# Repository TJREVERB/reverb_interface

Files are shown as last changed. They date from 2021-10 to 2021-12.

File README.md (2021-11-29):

# TJREVERB Interface Boards
Interface board rework, moved from Eagle to Kicad

The board provides power connections from the EPS and data connections from the flight computer to various components.

APRS and Iridium (through a MAX3232) are connected to UART, and can be selected between hardware UART and software/converter UART using jumpers. software/converter UART uses a converter as the primary UART device, with an option for software bit banging using RPi GPIO as a backup.

There are three branches: USB to UART, SPI to UART (DEPRECATED IN v1.4), and Multicore

The first is similar to the original design, and uses a USB to UART converter. 

The second uses an SPI to UART converter so that we can send data through the main Pi header instead of pogo pins or USB pads. DEPRECATED DUE TO DIFFICULTY IN SOFTWARE IMPLEMENTATION

The third uses an external AVR microcontroller as a secondary core, to be used for IO operations, specifically as an SPI/I2C to UART converter and an I2C buffer for sending delayed commands to the EPS (e.g. sending bus reset after a delay to give the pi enough time to exit script)

All branches include connections to bitbang uart instead of using the converter.

## Versions
v1.0 initial

v1.1 routing improvements

v1.2 fabricated first, received 10/24/21

v1.3 adds major corrections for circuitry

v1.4 introduces the new multicore branch

v1.5 replaces LSM9DS1 IMU with BNO055

v1.6 adds RTC and battery

v2.0 CAD compatibility check, fabbed as v2 on 11/28/21

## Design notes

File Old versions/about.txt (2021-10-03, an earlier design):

These were designed in eagle. Rev5 was fabricated and is currently in use in the flatsat.

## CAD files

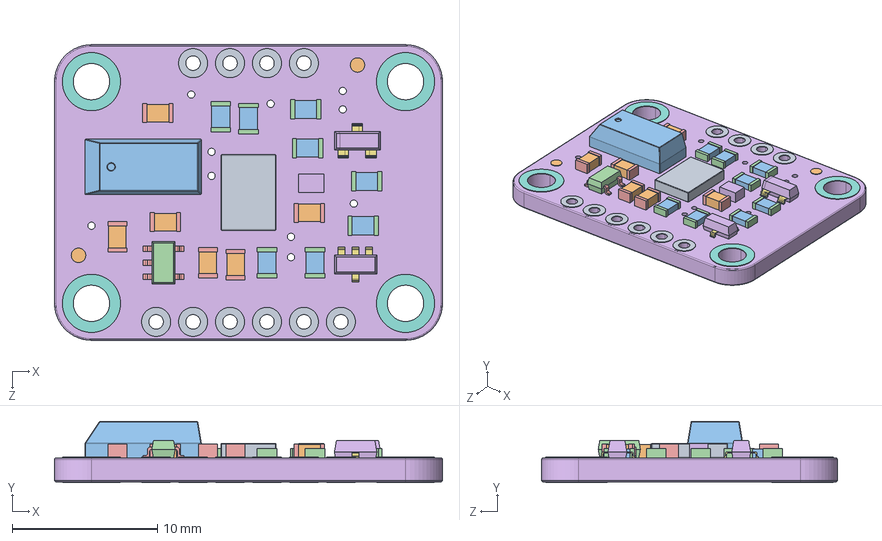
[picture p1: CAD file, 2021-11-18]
REVERB Interface Multicore/3D/Adafruit_BNO055_AP203.STEP
26.7 x 4.20 x 20.3 mm

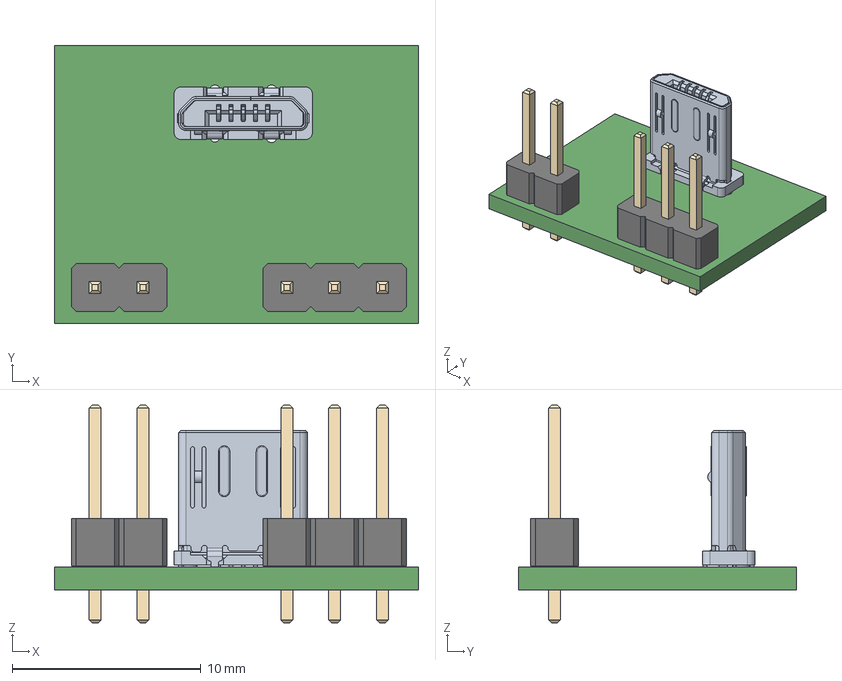
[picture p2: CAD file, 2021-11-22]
uUSB male BOB/uUSB male BOB.step
19.3 x 14.7 x 11.5 mm

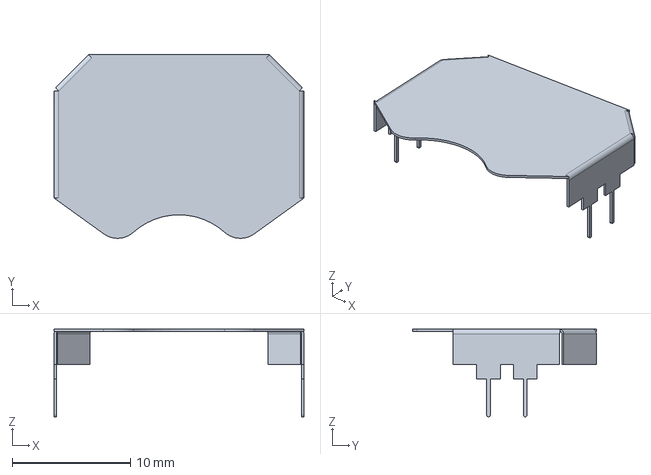
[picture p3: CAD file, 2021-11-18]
REVERB Interface Multicore/3D/Linx_-_BAT-HLD-001-THM.step
21.1 x 15.5 x 7.40 mm

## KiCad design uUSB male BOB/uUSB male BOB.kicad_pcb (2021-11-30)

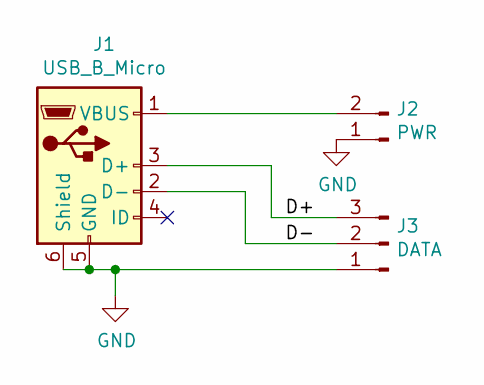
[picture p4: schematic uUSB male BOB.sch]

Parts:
J1: USB_B_Micro; USB3150-30-130-A
J2: PWR; PinHeader_1x02_P2.54mm_Vertical
J3: DATA; PinHeader_1x03_P2.54mm_Vertical

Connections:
/D+: J1.3 (D+), J3.3
/D-: J1.2 (D-), J3.2
GND: J1.5 (GND), J1.6 (Shield), J2.1, J3.1
unnamed: J1.1 (VBUS), J2.2

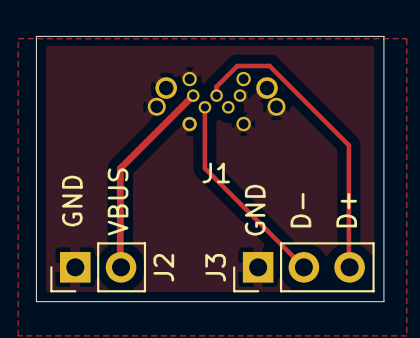
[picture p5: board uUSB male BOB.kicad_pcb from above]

Board: 2 copper layers, 19.3 x 14.7 mm, 3 parts (0 on the bottom side), 4 nets.

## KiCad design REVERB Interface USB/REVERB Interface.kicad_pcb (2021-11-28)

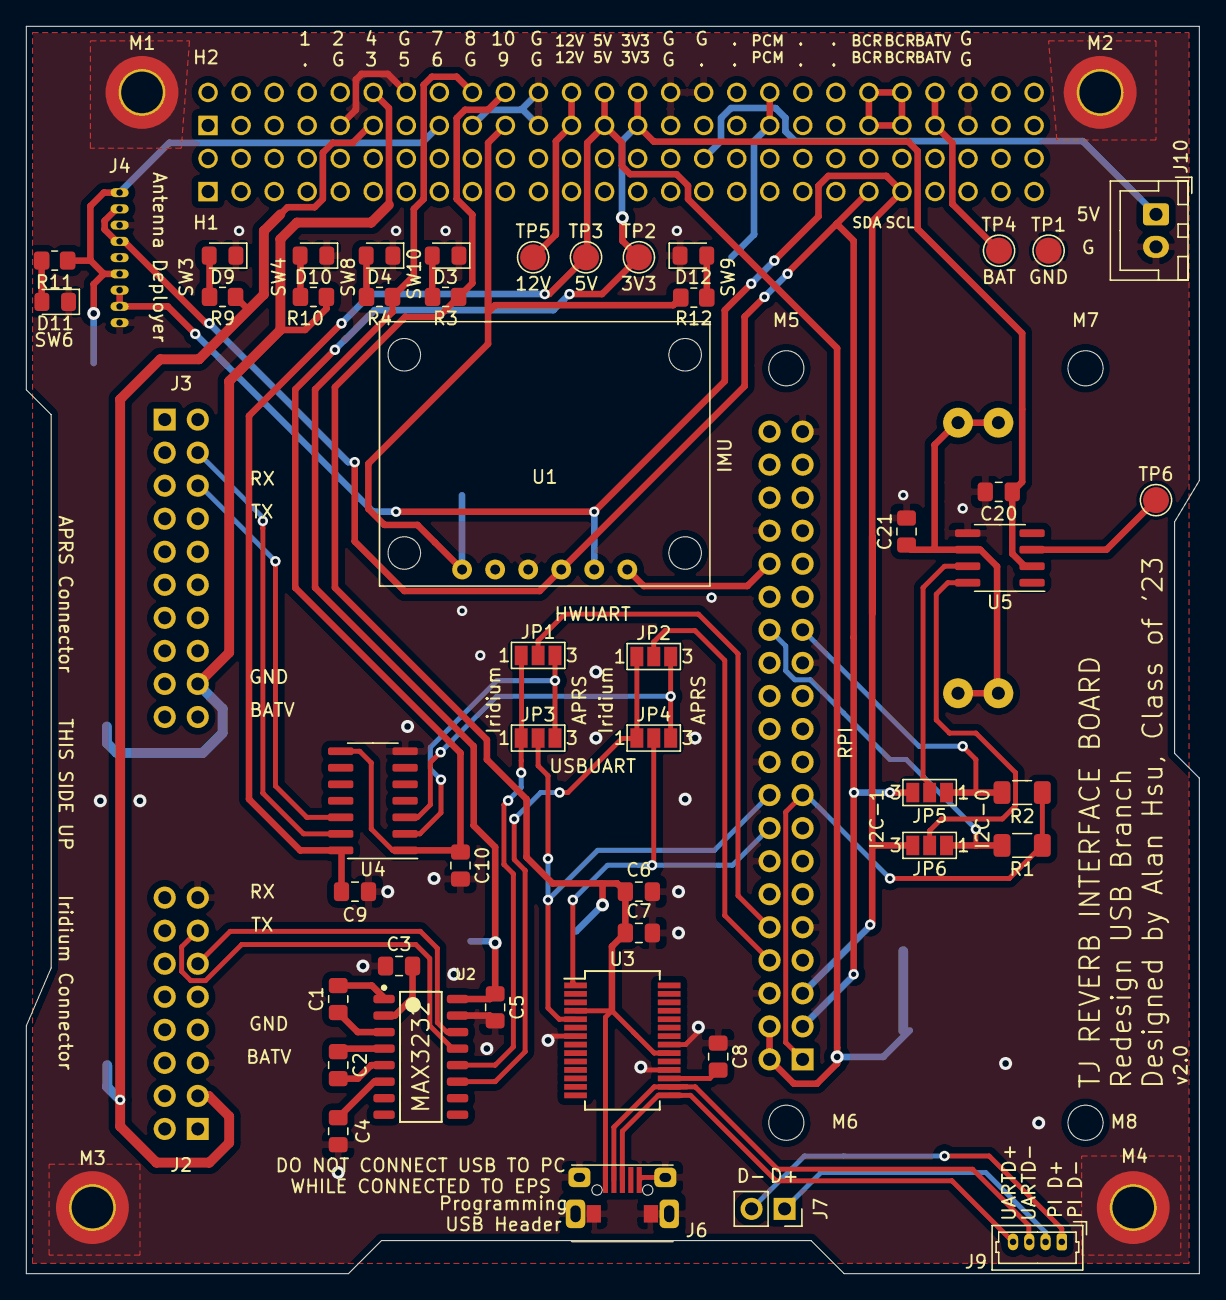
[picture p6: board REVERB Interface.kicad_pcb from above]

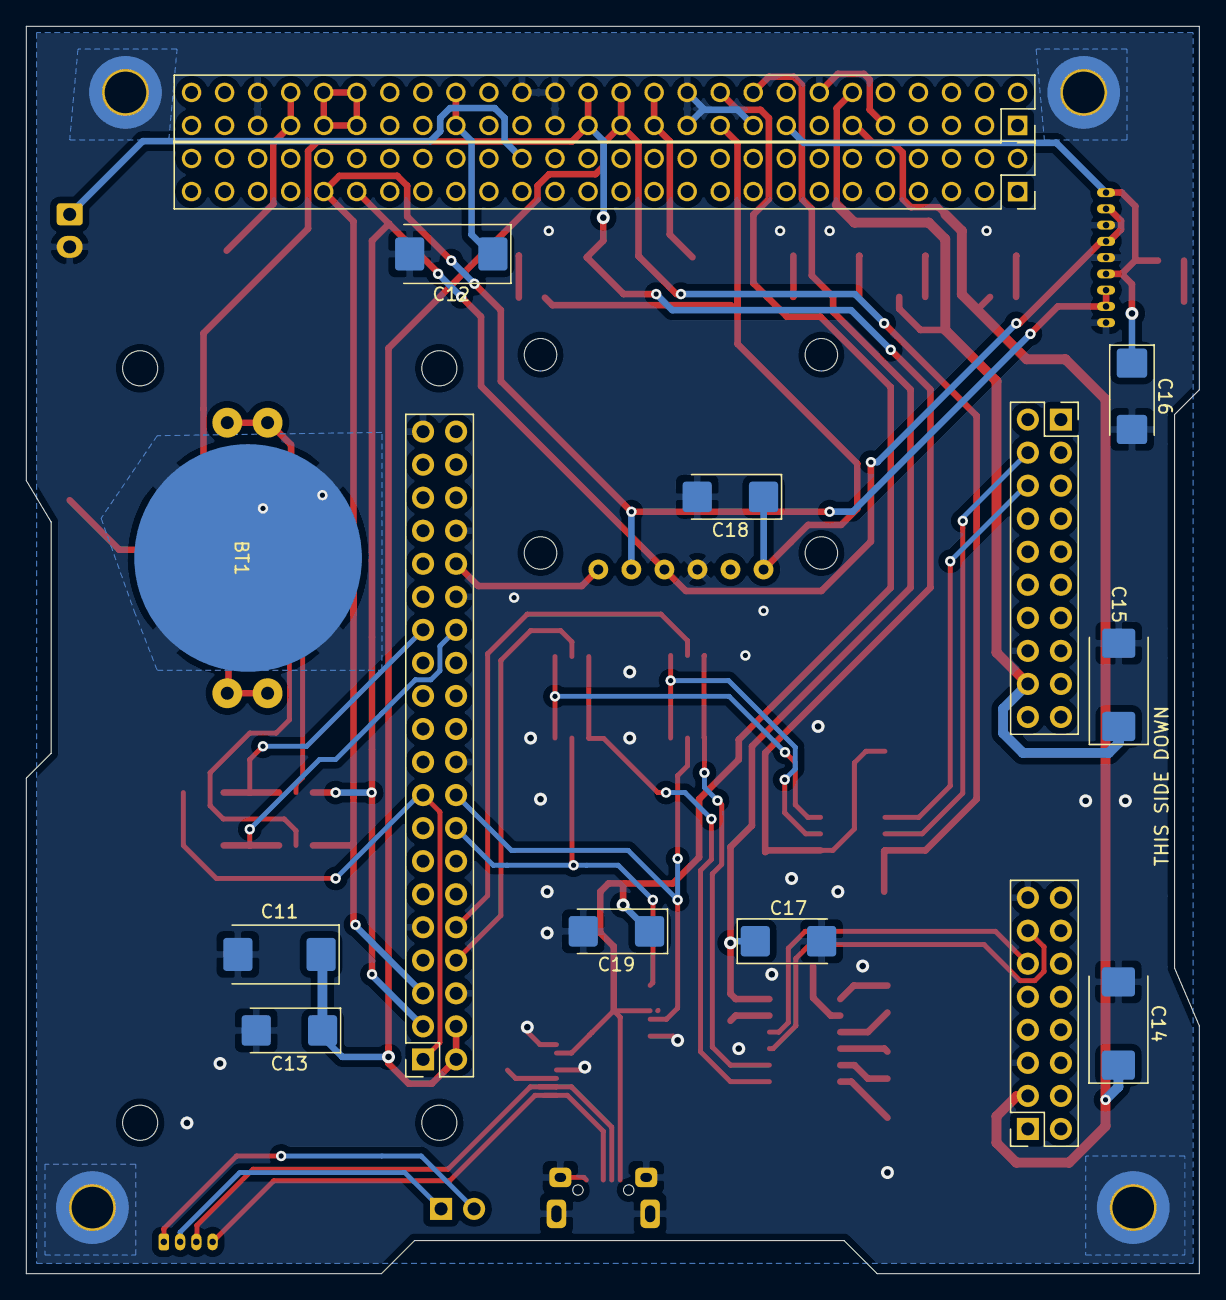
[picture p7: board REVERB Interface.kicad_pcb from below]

Board: 2 copper layers, 90.2 x 95.9 mm, 71 parts (15 on the bottom side), 53 nets.

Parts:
BT1: CR-2032; CR2032-LINX-HLD-001-THM
C1, C5, C7, C9, C10: 0.1uF; C_0805_2012Metric_Pad1.18x1.45mm_HandSolder
C2, C3, C4: 0.47uF; C_0805_2012Metric_Pad1.18x1.45mm_HandSolder
C6: 4.7uF; C_0805_2012Metric_Pad1.18x1.45mm_HandSolder
C8, C20, C21: 1uF; C_0805_2012Metric_Pad1.18x1.45mm_HandSolder
C11, C12, C14, C15: 100uF; CP_EIA-7343-43_Kemet-X_Pad2.25x2.55mm_HandSolder
C13, C16, C17, C18, C19: 22uF; CP_EIA-6032-28_Kemet-C_Pad2.25x2.35mm_HandSolder
D3, D4, D9, D10, D11, D12: RED; LED_0805_2012Metric_Pad1.15x1.40mm_HandSolder
H1: EPS Stack Header 2; PinSocket_2x26_P2.54mm_Vertical
H2: EPS Stack Header 1; PinSocket_2x26_P2.54mm_Vertical
J1: RPiZeroW; PinSocket_2x20_P2.54mm_Vertical
J2: Iridium; PinSocket_2x08_P2.54mm_Vertical
J3: APRS; PinSocket_2x10_P2.54mm_Vertical
J4: Antenna; 1.25mmPitchHeader
J6: USB_B_Micro; AdafruitMicroB
J7: USB; PinSocket_1x02_P2.54mm_Vertical
J9: USB SWITCH; Molex_PicoBlade_53047-0410_1x04_P1.25mm_Vertical
J10: USBPWR; JST_XH_B2B-XH-A_1x02_P2.50mm_Vertical
JP1: HWRX; SolderJumper-3_P1.3mm_Open_Pad1.0x1.5mm_NumberLabels
JP2: HWTX; SolderJumper-3_P1.3mm_Open_Pad1.0x1.5mm_NumberLabels
JP3: USBUARTRX; SolderJumper-3_P1.3mm_Open_Pad1.0x1.5mm_NumberLabels
JP4: USBUARTTX; SolderJumper-3_P1.3mm_Open_Pad1.0x1.5mm_NumberLabels
JP5: RTCSDA; SolderJumper-3_P1.3mm_Open_Pad1.0x1.5mm_NumberLabels
JP6: RTCSCL; SolderJumper-3_P1.3mm_Open_Pad1.0x1.5mm_NumberLabels
M1, M2, M3, M4: Stack Mounting Hole; MountingHole_3.2mm_M3_DIN965_Pad_TopBottom
M5, M6, M7, M8: PiMount; MountingHole_2.7mm_M2.5
R1, R2: 2.2K; R_1206_3216Metric_Pad1.30x1.75mm_HandSolder
R3, R4, R11, R12: 1K; R_0805_2012Metric_Pad1.20x1.40mm_HandSolder
R9, R10: 5K; R_0805_2012Metric_Pad1.20x1.40mm_HandSolder
TP1: GND; TestPoint_Pad_D2.0mm
TP2: 3V3; TestPoint_Pad_D2.0mm
TP3: 5V; TestPoint_Pad_D2.0mm
TP4: BAT; TestPoint_Pad_D2.0mm
TP5: 12V; TestPoint_Pad_D2.0mm
TP6: SQWV; TestPoint_Pad_D2.0mm
U1: IMU; BNO055
U2: MAX3232; Texas_Instruments-MAX3232ID-Level_A
U3: CY7C65213-28PVXI; SSOP-28_5.3x10.2mm_P0.65mm
U4: TXB0104D; SOIC-14_3.9x8.7mm_P1.27mm
U5: DS3232M; SOIC-8_3.9x4.9mm_P1.27mm

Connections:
+3.3VA: J1.1, J1.17, R1.1, R2.1
+3V3: C10.1, C20.1, H2.27, H2.28, TP2.1, U4.1, U4.8, U5.2
+5V: C9.1, C11.1, C13.1, H2.25, H2.26, J1.2, J1.4, TP3.1, U4.14
+12V: H2.23, H2.24, TP5.1
+BATT: BT1.1, C21.1, U5.6
/5VUSBCHG: H1.32, J10.1
/APRSRX: JP1.3, JP3.3, U4.2
/APRSRX_Shift: J3.4, U4.13
/APRSTX: JP2.3, JP4.3, U4.3
/APRSTX_Shift: J3.6, U4.12
/BCR_OUT: H2.41, H2.42, H2.43, H2.44
/D+: J6.3, J9.4, U3.15
/D-: J6.2, J9.3, U3.16
/EPSSCL: H1.43, J1.5, J4.7, J4.8, JP6.3, U1.5
/EPSSDA: H1.41, J1.3, J4.2, J4.4, JP5.3, U1.4
/HWRX: J1.10, JP1.2
/HWTX: J1.8, JP2.2
/IMURST: J1.32, U1.6
/PCM_IN: C12.1, H2.35, H2.36
/PID+: J7.1, J9.2
/PID-: J7.2, J9.1
/R1IN: J2.13, U2.13
/R1OUT: JP1.1, JP3.1, U2.12
/RTCSCL: JP6.2, U5.8
/RTCSDA: JP5.2, U5.7
/SCL0: J1.28, JP6.1, R1.2
/SDA0: J1.27, JP5.1, R2.2
/SQW: TP6.1, U5.3
/SW3: C14.1, H2.11, J2.3, R9.1
/SW4: C15.1, H2.12, J3.18, R10.1
/SW6: C16.1, H2.15, J4.1, J4.6, R11.1
/SW8: C5.1, C17.1, H2.18, R4.1, U2.16
/SW9: C18.1, H2.19, R12.1, U1.1
/SW10: C6.1, C7.1, C19.1, H2.20, J6.1, R3.1, U3.4, U3.20
/T1IN: JP2.1, JP4.1, U2.11
/T1OUT: J2.11, U2.14
/USBUARTRX: J1.18, JP3.2, U3.5
/USBUARTTX: J1.16, JP4.2, U3.1
GND: BT1.2, C3.1, C4.1, C5.2, C6.2, C7.2, C8.2, C9.2, C10.2, C11.2, C12.2, C13.2, C14.2, C15.2, C16.2, C17.2, C18.2, C19.2, C20.2, C21.2, D3.1, D4.1, D9.1, D10.1, D11.1, D12.1, H2.9, H2.14, H2.17, H2.21, H2.22, H2.29, H2.30, H2.32, H2.47, H2.48, J1.6, J1.9, J1.14, J1.20, J1.25, J1.30, J1.34, J1.39, J2.5, J2.15, J3.16, J4.3, J4.5, J4.9, J6.5, J6.6, J10.2, M1.1, M2.1, M3.1, M4.1, TP1.1, U1.3, U2.15, U3.7, U3.18, U3.21, U4.7, U5.5
unnamed: C1.1, U2.3
unnamed: C1.2, U2.1
unnamed: C2.1, U2.4
unnamed: C2.2, U2.5
unnamed: C3.2, U2.2
unnamed: C4.2, U2.6
unnamed: C8.1, U3.17
unnamed: D3.2, R3.2
unnamed: D4.2, R4.2
unnamed: D9.2, R9.2
unnamed: D10.2, R10.2
unnamed: D11.2, R11.2
unnamed: D12.2, R12.2
VBUS: H2.45, H2.46, TP4.1

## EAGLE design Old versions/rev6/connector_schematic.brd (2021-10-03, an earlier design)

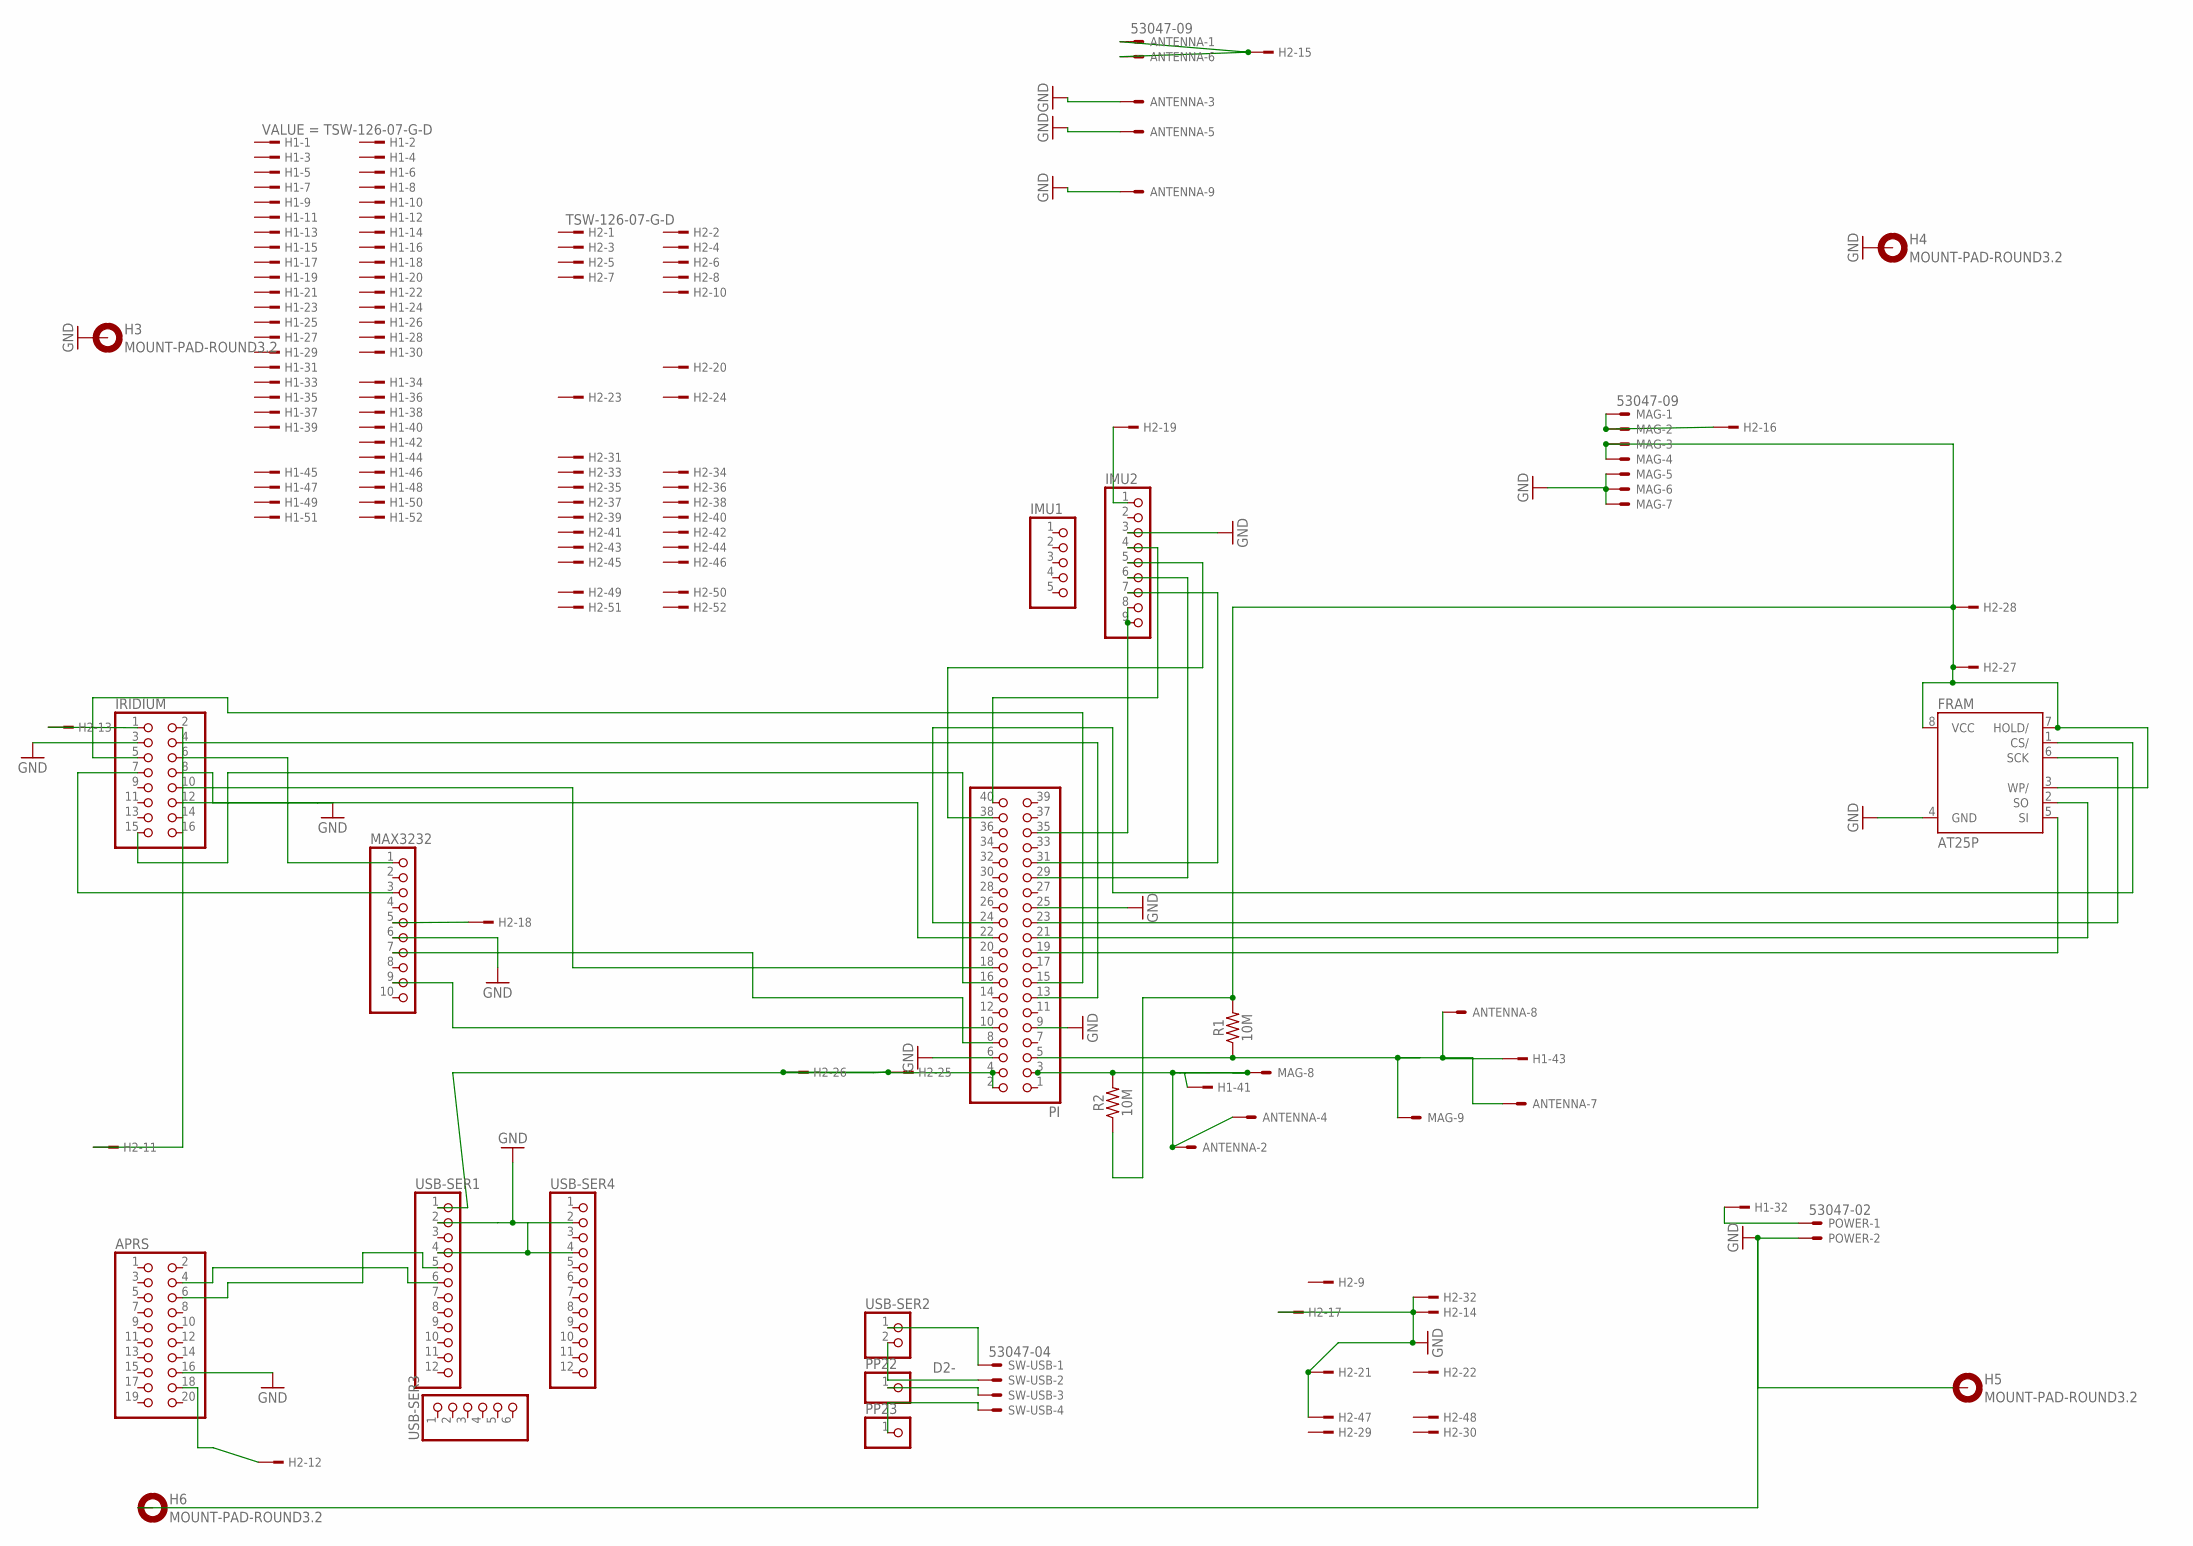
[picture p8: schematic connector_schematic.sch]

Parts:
ANTENNA: 53047-09
APRS: PINHD-2X10; 2X10
FRAM: AT25P; DIL08
H1, H2: TSW-126-07-G-D; TSW-126-XX-G-D
H3, H4, H5, H6: MOUNT-PAD-ROUND3.2; 3,2-PAD
IMU1: PINHD-1X5; 1X05
IMU2: PINHD-1X9; 1X09
IRIDIUM: PINHD-2X8; 2X08
MAG: 53047-09
MAX3232: PINHD-1X10; 1X10
PI: PINHD-2X20; 2X20
POWER: 53047-02
PP22, PP23: PINHD-1X1; 1X01
R1, R2: 10M; AXIAL-0.3
SW-USB: 53047-04
USB-SER1, USB-SER4: PINHD-1X12; 1X12
USB-SER2: PINHD-1X2; 1X02
USB-SER3: PINHD-1X6; 1X06

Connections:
3V3: FRAM.3 (WP/), FRAM.7 (HOLD/), FRAM.8 (VCC), H2.27, H2.28, MAG.3, MAG.4, R1.P$2 (2), R2.P$1 (1)
5V: H2.25, H2.26, PI.2, PI.4, USB-SER1.1
D2+: SW-USB.1, USB-SER2.1
D2-: SW-USB.2, USB-SER2.2
D+: PP22.1, SW-USB.3
D-: PP23.1, SW-USB.4
GND: ANTENNA.3, ANTENNA.5, ANTENNA.9, APRS.16, FRAM.4 (GND), H2.14, H2.17, H2.21, H2.32, H2.47, H3.B3,2, H4.B3,2, H5.B3,2, H6.B3,2, IMU2.3, IRIDIUM.3, IRIDIUM.8, MAG.5, MAG.6, MAG.7, MAX3232.6, PI.6, PI.9, PI.25, POWER.2, USB-SER1.2, USB-SER1.4, USB-SER4.2, USB-SER4.4
unnamed: APRS.18, H2.12
unnamed: IMU2.5, PI.38
unnamed: APRS.6, USB-SER1.5
unnamed: H2.19, IMU2.1
unnamed: ANTENNA.1, ANTENNA.6, H2.15
unnamed: H2.13, IRIDIUM.1
unnamed: IRIDIUM.4, PI.13
unnamed: IRIDIUM.5, PI.15
unnamed: IRIDIUM.15, PI.16
unnamed: IRIDIUM.10, PI.18
unnamed: MAX3232.7, PI.8
unnamed: H1.32, POWER.1
unnamed: APRS.4, USB-SER1.6
unnamed: IRIDIUM.12, PI.22
unnamed: H2.11, IRIDIUM.2
unnamed: FRAM.5 (SI), PI.19
unnamed: FRAM.6 (SCK), PI.23
unnamed: FRAM.1 (CS/), PI.24
unnamed: FRAM.2 (SO), PI.21
unnamed: MAX3232.9, PI.10
unnamed: IRIDIUM.6, MAX3232.1
unnamed: IRIDIUM.7, MAX3232.3
unnamed: IMU2.4, PI.40
unnamed: IMU2.6, PI.29
unnamed: IMU2.7, PI.31
unnamed: IMU2.8, IMU2.9, PI.35
unnamed: H2.16, MAG.1, MAG.2
unnamed: H2.18, MAX3232.5
SCL: ANTENNA.7, ANTENNA.8, H1.43, MAG.9, PI.5, R1.P$1 (1)
SDA: ANTENNA.2, ANTENNA.4, H1.41, MAG.8, PI.3, R2.P$2 (2)

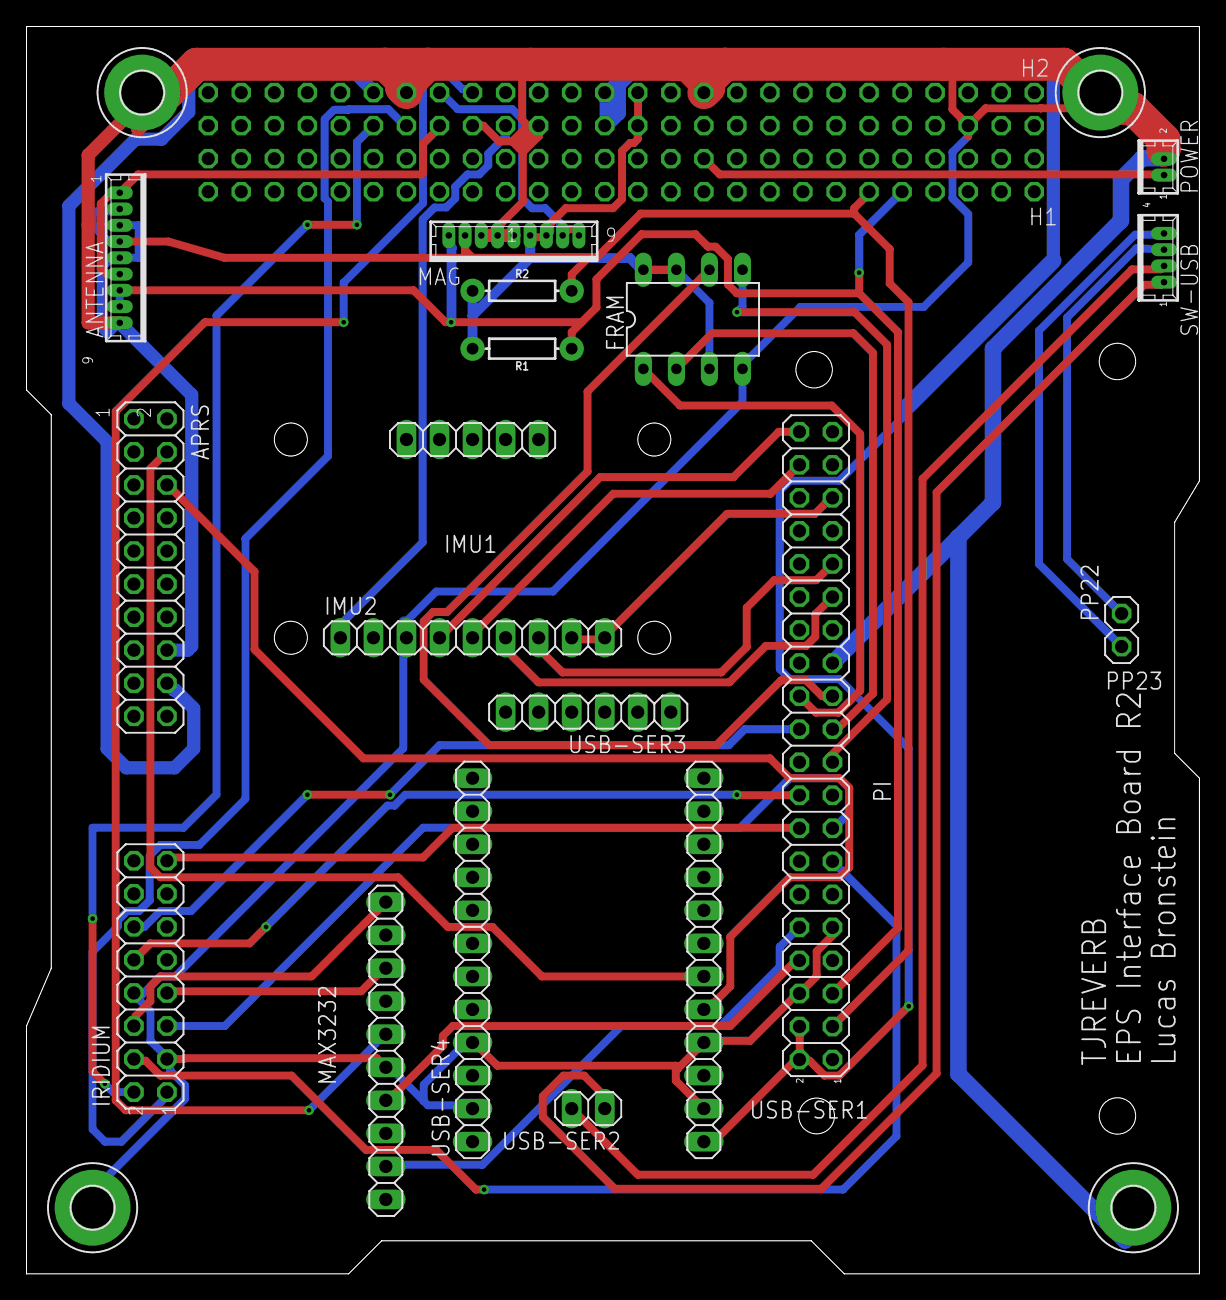
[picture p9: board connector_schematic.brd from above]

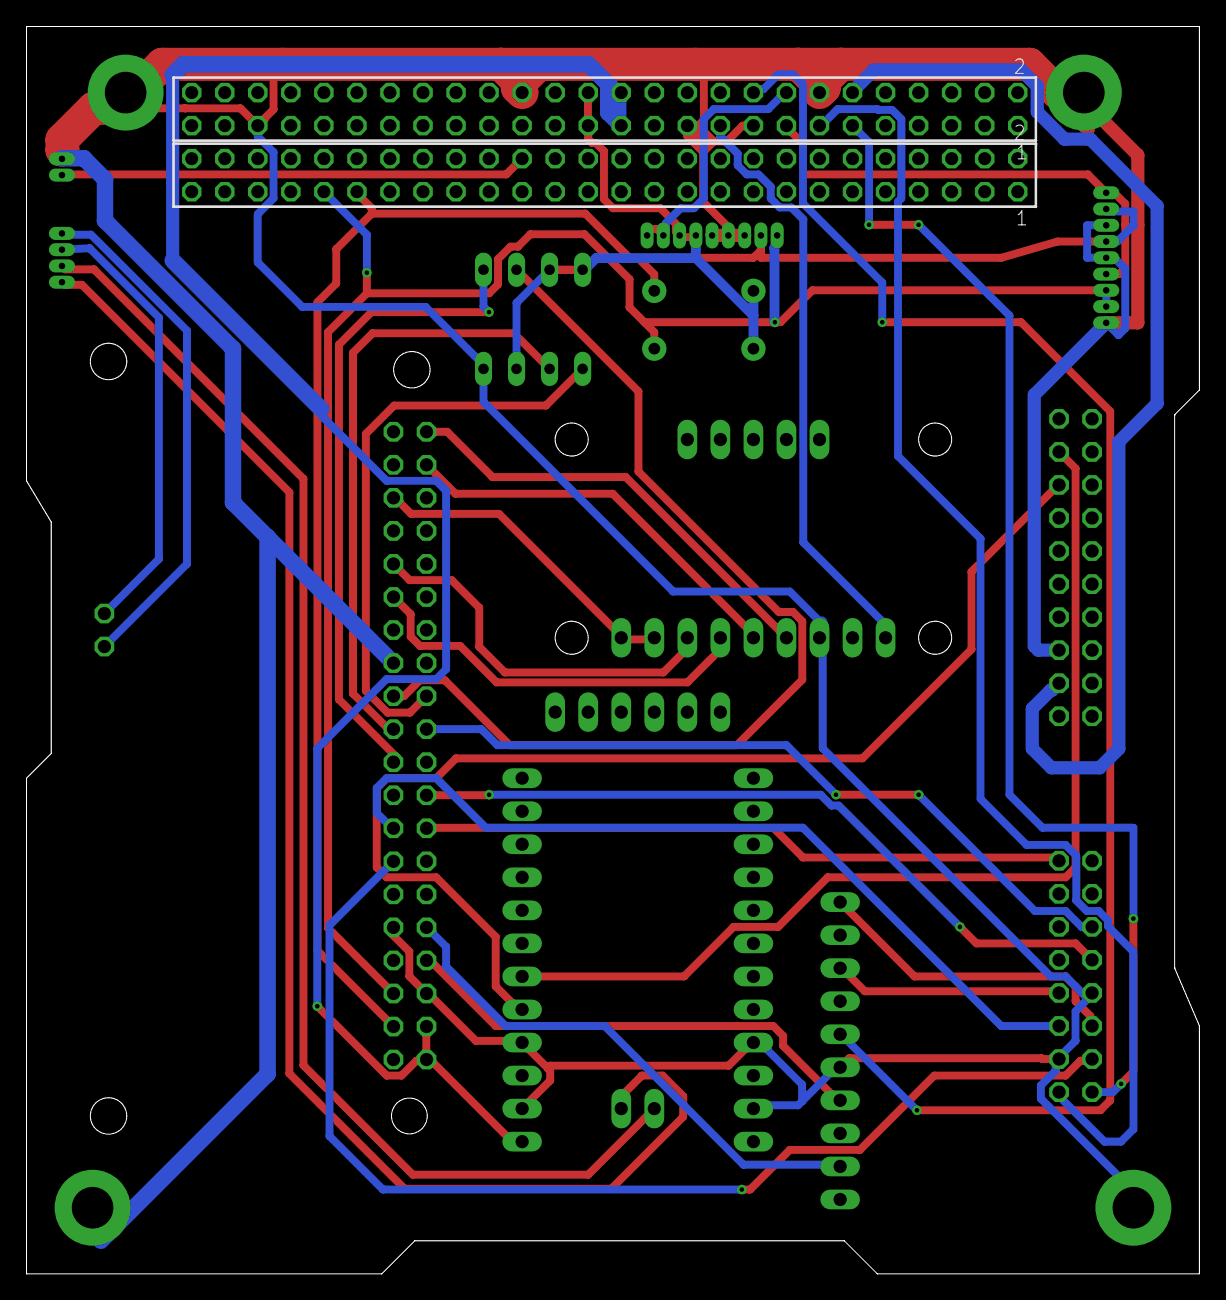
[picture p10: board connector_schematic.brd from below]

Board: 2 copper layers, 90.2 x 95.9 mm, 25 parts (2 on the bottom side), 37 nets.

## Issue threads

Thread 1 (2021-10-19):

APRS Logic Level

Alan-JH, 2021-10-19:
APRS uses 5V logic levels, whereas the board design's converters and the pi itself (if hardware uart option is selected) run at 3v3. Previously this was solved by running the usb to uart at 5v, but with the option of different adapters, it may be better to introduce a logic level shifter.

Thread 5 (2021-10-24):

Silkscreen spacing

Alan-JH, 2021-10-24:
APRS and Iridium silkscreen labels may be too close to the pins

Closed 2021-11-03.

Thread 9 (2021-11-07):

Add BNO055 compatibility

Alan-JH, 2021-11-07:
LSM9DS1 is out of stock everywhere, BNO055 is more common

Alan-JH, 2021-11-08:
Added combined BNO055 and LSM9DS1 footprint, but the SDA and SCL lines on the BNO055 is swapped from the LSM9DS1, so we need to decide between one or the other.

Closed 2021-11-12.

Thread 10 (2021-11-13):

replace jumpers with dip switches

Alan-JH, 2021-11-13:

Closed 2021-11-15.

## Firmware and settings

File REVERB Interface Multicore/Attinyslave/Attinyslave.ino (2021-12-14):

#include <SPI.h>
#include <Wire.h>

byte outbuf[255];
byte pos = 0;

void setup() {
  Wire.begin(0x45); //Begin IIC slave
  Wire.onReceive (receiveEvent); //Interrupt flag
  Serial.begin(19200); //Begin uart
}

void receiveEvent(int len){
  byte mode = Wire.read();
  if (mode == 0){ //UART transmit
    byte b = Wire.read();
    Serial.write(b);
  }else if (mode == 1){ //Transmit UART receive buffer
    if (--pos < 0){
      pos = 254;
    }
    Wire.write(outbuf[pos]);
  }else if (mode == 2){ //I2C Delay: First byte delay in 100ms intervals, Second byte command, third byte data
    byte t = Wire.read();
    delay(t * 100);
    Wire.beginTransmission(0x2b);
    Wire.write(0x70);
    Wire.write(0x0F);
    Wire.endTransmission();
  }
}

void loop() {
  if (Serial.available()){ //Read in to buffer, add to pointer
    outbuf[pos++] = Serial.read();
  }
}

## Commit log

2021-10-03 Establish file structure, add archived versions
    [REVERB Interface.kicad_pcb, REVERB Interface.sch, connector_schematic (1).sch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]
2021-10-03 Schematic work: added EPS and Pi Headers
    [REVERB Interface.sch]
2021-10-03 mounting holes and ground connections
    [REVERB Interface.sch]
2021-10-06 add capacitors to max3232
    [REVERB Interface.sch]
2021-10-06 wiring work
    [REVERB Interface.sch]
2021-10-07 footprint associations
    [REVERB Interface.sch]
2021-10-07 create board, finish footprint association
    [REVERB Interface.kicad_pcb, REVERB Interface.sch]
2021-10-07 copy old board layout positions
    [REVERB Interface.kicad_pcb, REVERB Interface.sch]
2021-10-07 silkscreen labels
    [REVERB Interface.kicad_pcb]
2021-10-07 do stuff
    [REVERB Interface.kicad_pcb, REVERB Interface.sch]
2021-10-09 bunch of work
    [REVERB Interface.kicad_pcb, REVERB Interface.sch]
2021-10-09 add solder jumpers
    [REVERB Interface.kicad_pcb, REVERB Interface.sch]
2021-10-09 routing work
    [REVERB Interface.kicad_pcb, REVERB Interface.sch]
2021-10-10 Update REVERB Interface.kicad_pcb
    [REVERB Interface.kicad_pcb]
2021-10-10 finsihing up routing
    [REVERB Interface.kicad_pcb]
2021-10-10 finishing up for real now
    [REVERB Interface-B_Cu.gbr, REVERB Interface-B_Mask.gbr, REVERB Interface-B_Paste.gbr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]
2021-10-10 create spi to uart branch
    [REVERB Interface-B_Cu.gbr, REVERB Interface-B_Mask.gbr, REVERB Interface-B_Paste.gbr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]
2021-10-10 fix a via
    [REVERB Interface-B_Cu.gbr, REVERB Interface-B_Mask.gbr, REVERB Interface-B_Paste.gbr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]
2021-10-10 Add LDO to convert 5V USB logic to 3V3 UART
    [REVERB Interface-B_Cu.gbr, REVERB Interface-B_Mask.gbr, REVERB Interface-B_Paste.gbr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]
2021-10-10 fix silkscreen, add another ground via
    [REVERB Interface-B_Cu.gbr, REVERB Interface-B_Mask.gbr, REVERB Interface-B_Paste.gbr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]
2021-10-10 spi edits
    [REVERB Interface.kicad_pcb, REVERB Interface.sch]
2021-10-10 Update REVERB Interface.sch
    [REVERB Interface.sch]
2021-10-10 SPI Branch routing
    [REVERB Interface-B_Cu.gbr, REVERB Interface-B_Mask.gbr, REVERB Interface-B_Paste.gbr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]
2021-10-10 update silkscreen
    [REVERB Interface-B_Cu.gbr, REVERB Interface-B_Mask.gbr, REVERB Interface-B_Paste.gbr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]
2021-10-10 Add RTS and CTS connections to layout
    [REVERB Interface-B_Cu.gbr, REVERB Interface-B_Mask.gbr, REVERB Interface-B_Paste.gbr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]
2021-10-11 Add LEDs for all used PDMs
    [REVERB Interface-B_Cu.gbr, REVERB Interface-B_Mask.gbr, REVERB Interface-B_Paste.gbr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]
2021-10-13 visual cleanup
    [REVERB Interface.sch]
2021-10-13 Remove LDO
    [REVERB Interface-B_Cu.gbr, REVERB Interface-B_Mask.gbr, REVERB Interface-B_Paste.gbr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]
2021-10-13 Add note regarding usb programming
    [REVERB Interface.sch]
2021-10-14 Routing EMI considerations
    [REVERB Interface-B_Cu.gbr, REVERB Interface-B_Mask.gbr, REVERB Interface-B_Paste.gbr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]
2021-10-15 EMI and SI minmaxing, round 2
    [REVERB Interface-B_Cu.gbr, REVERB Interface-B_Mask.gbr, REVERB Interface-B_Paste.gbr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]
2021-10-15 Combined files for smt stencil
    *NOT PANELIZED*
    [Combined boards for stencil-B_Cu.gbr, Combined boards for stencil-B_Mask.gbr, Combined boards for stencil-B_Paste.gbr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]
2021-10-15 Replace max3232 footprint, update stencil
    [Combined boards for stencil-B_Cu.gbr, Combined boards for stencil-B_Mask.gbr, Combined boards for stencil-B_Paste.gbr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]
2021-10-15 update silkscreen again
    [REVERB Interface-B_Cu.gbr, REVERB Interface-B_Mask.gbr, REVERB Interface-B_Paste.gbr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]
2021-10-24 Remove incorrect uart flow control connections, pull CTS low. Improve silkscreen placement
    Issue #3 and Issue #5
    [REVERB Interface.kicad_pcb, REVERB Interface.sch]
2021-10-24 Improve usb branch silkscreen, push v1.3
    #5 Will need to verify required clearance for connector housing later.
    [REVERB Interface.kicad_pcb]
2021-10-24 Add bitbang uart connections
    gpio 23 and 24, #2
    [REVERB Interface.kicad_pcb, REVERB Interface.sch]
2021-10-27 Add level shifters, updated sch revision numbers consistent with pcb
    [REVERB Interface.kicad_pcb, REVERB Interface.sch]
2021-10-28 add level shifter to routing
    #1
    [REVERB Interface-B_Cu.gbr, REVERB Interface-B_Mask.gbr, REVERB Interface-B_Paste.gbr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]
2021-11-03 Fix USB header placement
    [REVERB Interface-B_Cu.gbr, REVERB Interface-B_Mask.gbr, REVERB Interface-B_Paste.gbr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]
2021-11-03 add switch led silkscreen labels
    [REVERB Interface.kicad_pcb]
2021-11-04 Deprecate SPI branch, push v1.4, add new "multicore" branch, remove combined board files
    [Combined boards for stencil-B_Cu.gbr, Combined boards for stencil-B_Mask.gbr, Combined boards for stencil-B_Paste.gbr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]
2021-11-05 tie OE high
    [REVERB Interface.kicad_pcb, REVERB Interface.sch]
2021-11-06 Add decoupling
    [REVERB Interface-B_Cu.gbr, REVERB Interface-B_Mask.gbr, REVERB Interface-B_Paste.gbr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]
2021-11-08 fix imu implementation, add bno055 compatibility
    [REVERB Interface.kicad_pcb, REVERB Interface.sch]
2021-11-08 fix imu implementation on multicore branch
    [REVERB Interface.kicad_pcb, REVERB Interface.sch]
2021-11-11 intermediate commit
    [REVERB Interface.kicad_pcb, REVERB Interface.sch]
2021-11-12 finish bno055 mod, push v1.5
    [REVERB Interface.kicad_pcb, REVERB Interface.sch]
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2021-11-15 route, edit i2c description
    [REVERB Interface-B_Cu.gbr, REVERB Interface-B_Mask.gbr, REVERB Interface-B_Paste.gbr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]
2021-11-16 implement rtc on a pdm
    [REVERB Interface.kicad_pcb, REVERB Interface.sch]
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2021-11-17 fix some compile time errors
    [Attinyslave.ino]
2021-11-17 add footprints, may need to use smaller battery
    [REVERB Interface.kicad_pcb, REVERB Interface.sch]
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2021-11-21 add microusb breakout board
    [uUSB male BOB-B_Cu.gbr, uUSB male BOB-B_Mask.gbr, uUSB male BOB-B_Paste.gbr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]
2021-11-22 Move some parts around, remove UART LEDs, .step export, push v1.6
    [REVERB Interface-B_Cu.gbr, REVERB Interface-B_Mask.gbr, REVERB Interface-B_Paste.gbr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]
2021-11-26 start on adding i2c-0 option
    [REVERB Interface.kicad_pcb, REVERB Interface.sch]
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2021-11-26 tidy up the schematic, for usb branch
    [REVERB Interface.kicad_pcb, REVERB Interface.sch]
2021-11-26 finish tidying up schematics
    [REVERB Interface.kicad_pcb, REVERB Interface.sch]
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2021-11-30 move gerbers, add combined branches gerber again
    [Combined branches-B_Cu.gbr, Combined branches-B_Mask.gbr, Combined branches-B_Paste.gbr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]
2021-12-04 replace SPI slave with I2C slave
    [Attinyslave.ino]

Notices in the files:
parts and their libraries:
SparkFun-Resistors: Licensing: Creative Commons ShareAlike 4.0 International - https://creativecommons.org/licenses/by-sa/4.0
